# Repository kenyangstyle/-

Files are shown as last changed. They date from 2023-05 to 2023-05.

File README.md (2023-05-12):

# -
这是2023年华南理工大学机器人校内赛五山五狼—车车难造队的机械建模开源，我是本队机械建模队员 华南理工大学材料科学与工程学院 杨欣然。这次上传的车辆是自2023年2月得知赛题后便着手设计的，全部建模、图纸设计、加工联系任务和部分搭建任务由我完成。换句话说，我可以毫无任何内心压力的说我参与了前后两个队参赛的全过程，本车共有3代版本，每一代都是进行了相关的更新工作后进行，本次上传的便是第三代（也就是最终上场的车），十分不幸的是，由于一些完全超出本人能力的原因，最终上场参加2023-05-07和2023-05-13比赛的车与第三代车大相径庭。

底盘：
使用玻纤板，由4台545电机作为动力，橡胶轮4个，直径为96mm（未注明单位尺寸皆为毫米），前段为铲斗活动区，故仅在前后方安装铜柱；
中段与后段分别安装玻纤板作为连接，同时提供安装驱动板、电源板、电池等的空间，使用扎带固定电池/洞洞板
后段则安装了3D打印的滑梯，其中其高侧固定在铜柱、固定架上，低侧则搭在尾板舵机架（3D打印）上，作为承载木块的主要区域；尾板使用6mm玻纤板，在2台sg90舵机操作下进行移动，在规则改变后单独的舵机架被取消，舵机被固定在后方加固板上

抬升装置：
致敬VEX经典设计，但是玻纤板，前方用立柱（一个加工时给我带来了巨多麻烦的东西），大臂后方为齿轮组：2组4个20齿2模齿轮，其中下方2个齿轮与370电机D孔连接（这个主意现在来看蠢得一批），四个齿轮分别连接大臂上梁和小臂下梁，以抬升上方铲子。原计划小臂下梁使用活动滑梯版,承接铲子上的木块，后来由于改用铜柱加固，其已切割的板材被挪作他用。

铲子：铲子固定在抬升装置末端，用于提高位置，经过准确测量的铲子可完美覆盖3个矿区（如果抬升装置没bug的话），并通过一定角度顺利铲起木块，而在经过实际验证确认不可行后，在铲子两内侧加装了搂抱机构，可以将木块揽入其中，这一方案在实际测试中效果尚佳，但是对整体的电路稳定水平有较高要求。

取矿逻辑：车进入取矿区—车对准矿架—车抬起臂—铲子内机械臂揽入木块—机械臂抬升—铲子翻转90-130度，木块滑入活动滑梯版—木块从活动滑梯版划入固定滑梯板，并在碰撞尾板后停止-重复上述步骤到存储9-10个木块-车返回结算区-尾板翻转120-130度，木块凭借重力滑入并积分

反思：1、孔的设计：各个孔的尺寸并不统一，直接导致了在装车过程中零件（通用件）装配极为恶心，种类之繁多严重影响了我们的工作效率
      2、预留空间不足：整车设计上，由于几乎是贴着尺寸限制设计，许多原本在sw中显示无干涉的零件在实际装配和调试中纷纷出现干涉，最后不得不用角磨机处理
      3、零件选材：原本由于对行情不够了解，在设计底盘时选择L型铝，直接导致预算超标，被迫改设计改用玻纤，而在改图纸的过程中，由于对材料的不了解，预留孔位不够大，最后同样不得不上角磨机处理
      4、铲子：对矿物的错误理解直接导致了在测试过程中对木块的无能为力，而前段原本为铲起木块做的设计反而成为了破损的重灾区，幸运的是，铲面空间足够增加补救方案，遂加入2台舵机。
      5、储矿装置：同样出于对矿物的错误理解，使得矿物落入储矿机构后有掉落风险。但由于固定滑梯面和固定滑梯尾板是由3D打印制作，我们无法加高两侧防掉落机构，只能通过扎带进行软加固；同时原本的舵机臂设计由于舵机自身和规则改变的原因，先后剪短甚至弃用， 固定也最后选择打胶（正经的上热熔胶）。

未来改进：1、增加爬楼梯功能：由于时间关系，我们并没有安装爬楼梯的装置，而如果需要进行安装，完全可以在前轮电机和后轮电机中间加装2组4个伸缩电机，从而将前后轮组抬高
一半，从而上楼梯
          2、改用麦轮：原本寄希望于我们操作手的能力，但是在试车后认为麦轮还是有助于对准框架的，但是时间+尺寸原因导致其并未实现。
          3、铲子缩短：既然已经确认铲子无法铲木块，而必须要用揽的形式，则铲子也没必要做的过长，能放下舵机和揽入木块即可
          4、电机换成舵机：这是基于操作时难以控制升降臂两侧的电机同步行动而提出，实际上20kg360度舵机完全足够取代370电机，安装难度也有减小。
          5、统一孔径并加大预留空间：避免再出现由于各种尺寸螺丝螺母齐飞而导致的额外花费和效率低下，同时降低断孔概率

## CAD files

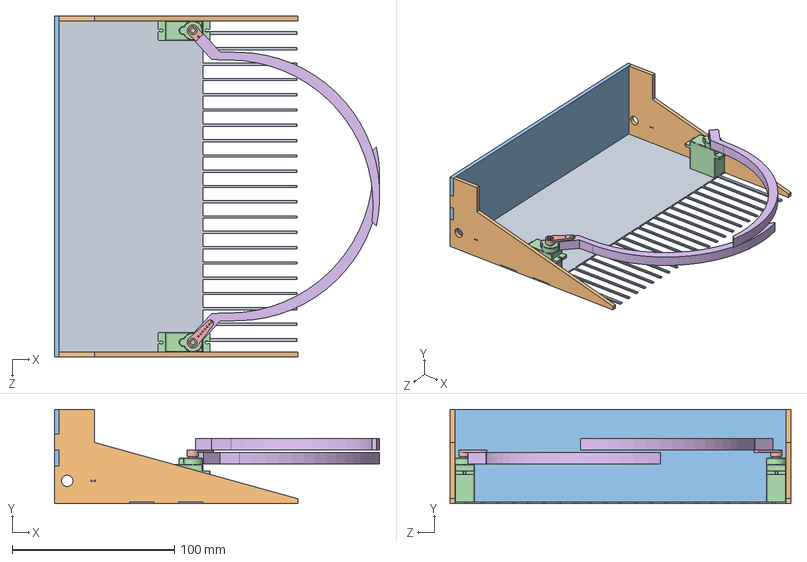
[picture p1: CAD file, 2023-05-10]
车车难造 最新机械开源/第二代应急铲子.SLDASM
200.4 x 58.0 x 210.0 mm
铲子 - 副本 (2)
铲子 - 副本 (3) x 2
铲子 - 副本
舵机 x 2
舵机臂 x 2
救急拉杆2 x 2

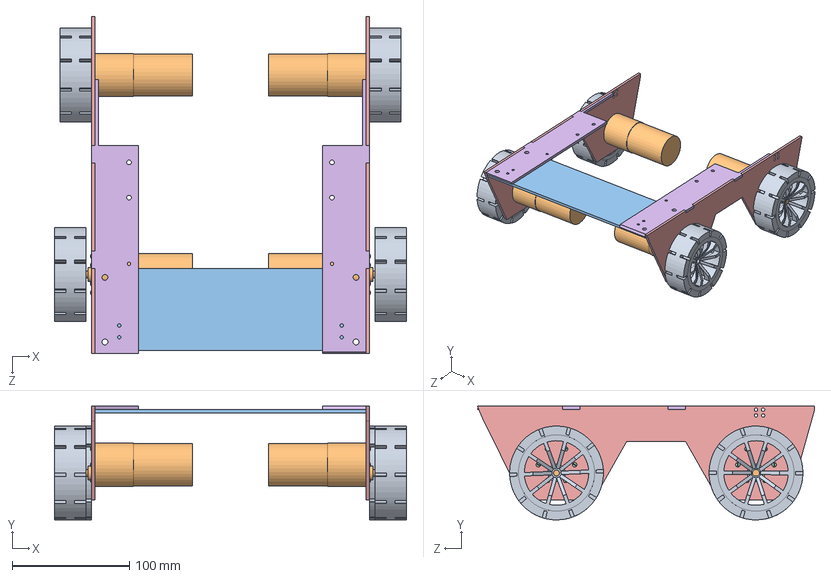
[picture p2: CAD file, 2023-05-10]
车车难造 最新机械开源/五山狼 第三代底盘原理.SLDASM
300.0 x 97.0 x 287.5 mm
teibielun x 4
545电机 x 4
下层结构加强
GB╱T 5284-1985[开槽半沉头自攻螺钉-F型ST2.2×6.5-F] x 24
L下插板 x 2
L上插板 x 2

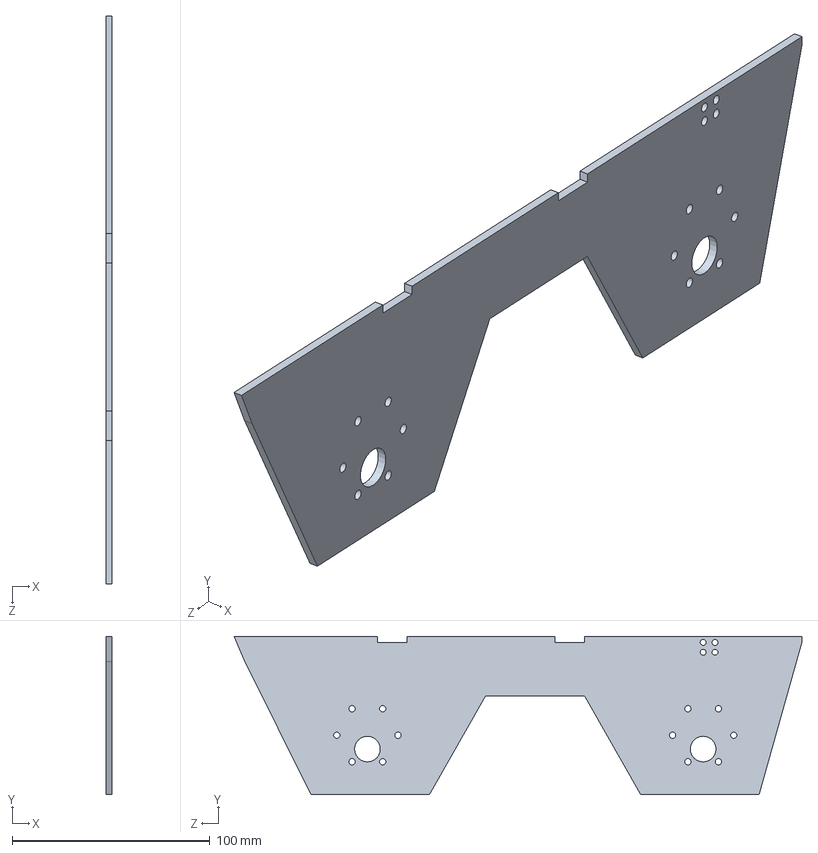
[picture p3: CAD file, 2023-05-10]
车车难造 最新机械开源/L--拼插板.SLDASM
3.00 x 80.0 x 287.5 mm

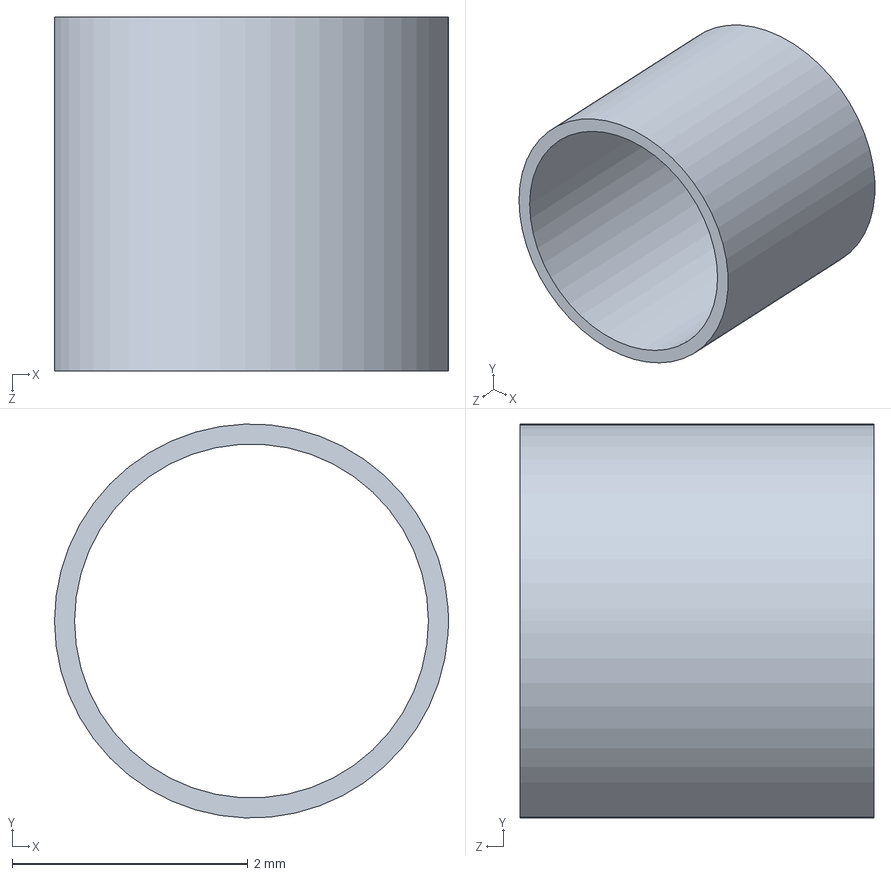
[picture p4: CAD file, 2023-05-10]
车车难造 最新机械开源/蠢得一批的轴套.SLDPRT
3.34 x 3.34 x 3.00 mm

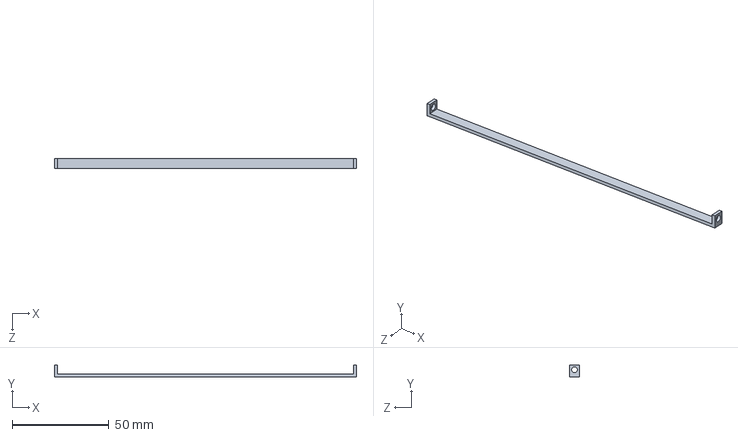
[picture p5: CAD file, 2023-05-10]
车车难造 最新机械开源/铝立柱（高.SLDPRT
156.0 x 6.00 x 5.00 mm

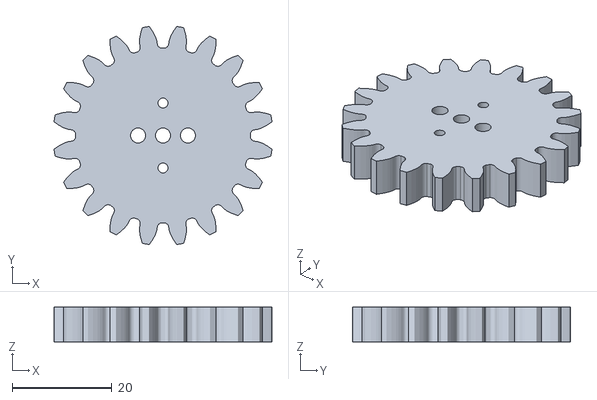
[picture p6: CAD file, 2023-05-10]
车车难造 最新机械开源/3代版本打印圆柱齿轮20×2.STL
43.7 x 43.7 x 7.00

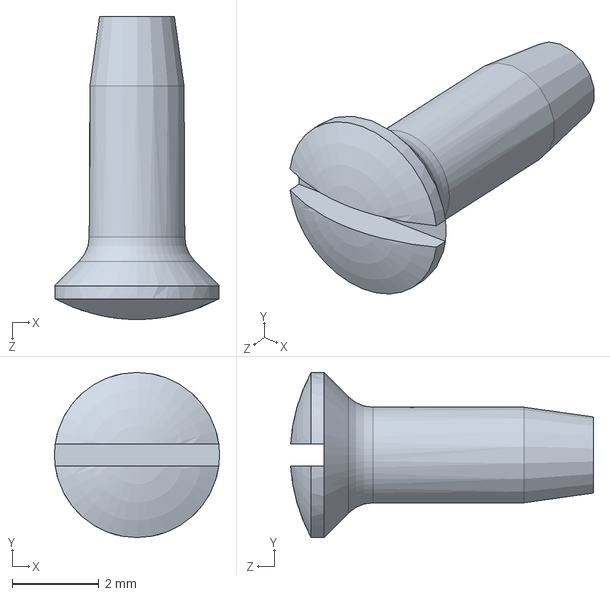
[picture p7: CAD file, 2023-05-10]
车车难造 最新机械开源/GB╱T 5284-1985[开槽半沉头自攻螺钉-F型ST2.2×6.5-F].sldprt
3.80 x 3.80 x 6.97 mm

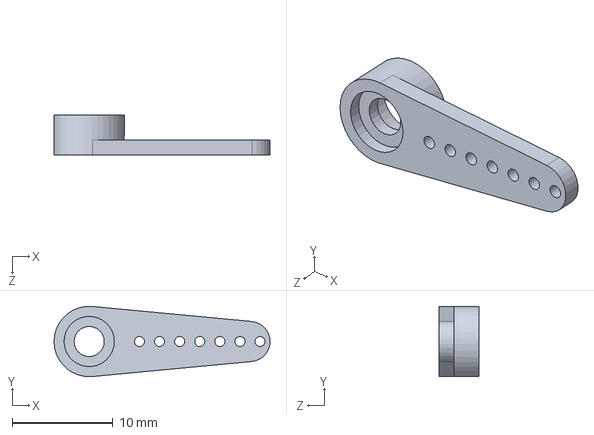
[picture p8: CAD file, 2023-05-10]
车车难造 最新机械开源/舵机臂.SLDPRT
21.5 x 6.99 x 4.00 mm

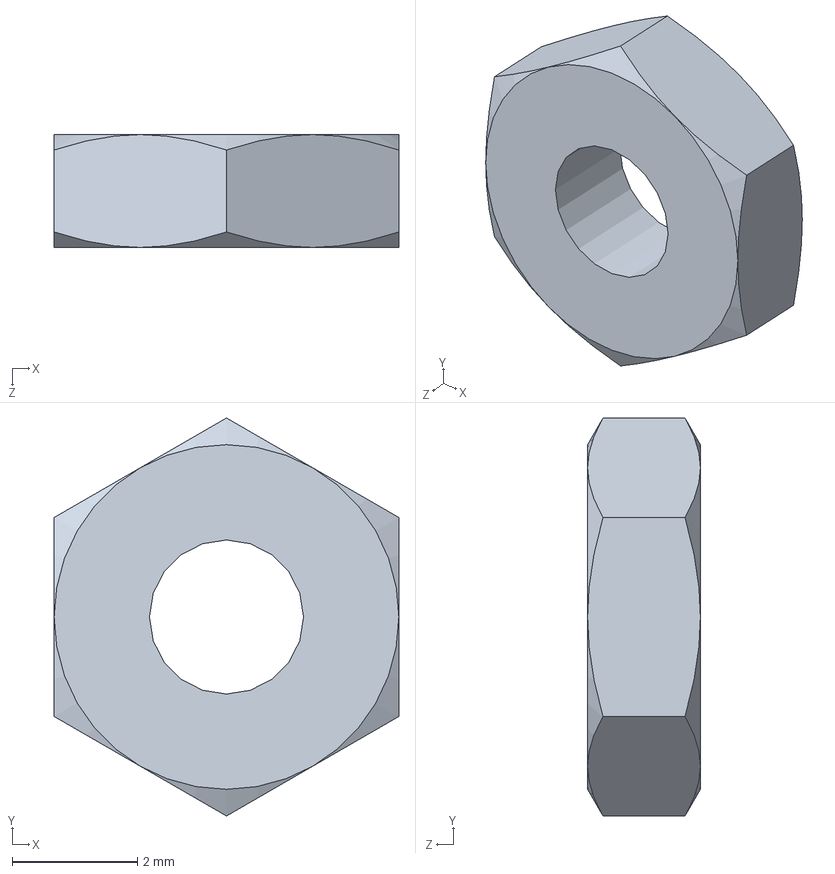
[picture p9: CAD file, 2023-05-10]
车车难造 最新机械开源/GB╱T 6172.1-2000[六角薄螺母 A级和B级M3].sldprt
5.50 x 6.35 x 1.80 mm

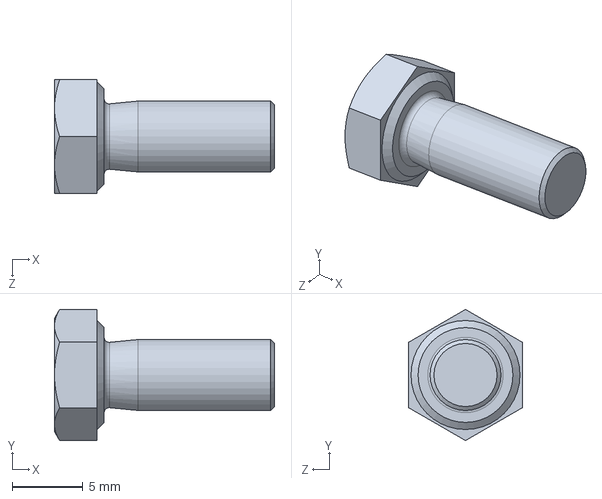
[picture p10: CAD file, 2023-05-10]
车车难造 最新机械开源/GB╱T 5783-2016[六角头螺栓 全螺纹M5×12].sldprt
15.5 x 9.24 x 8.00 mm

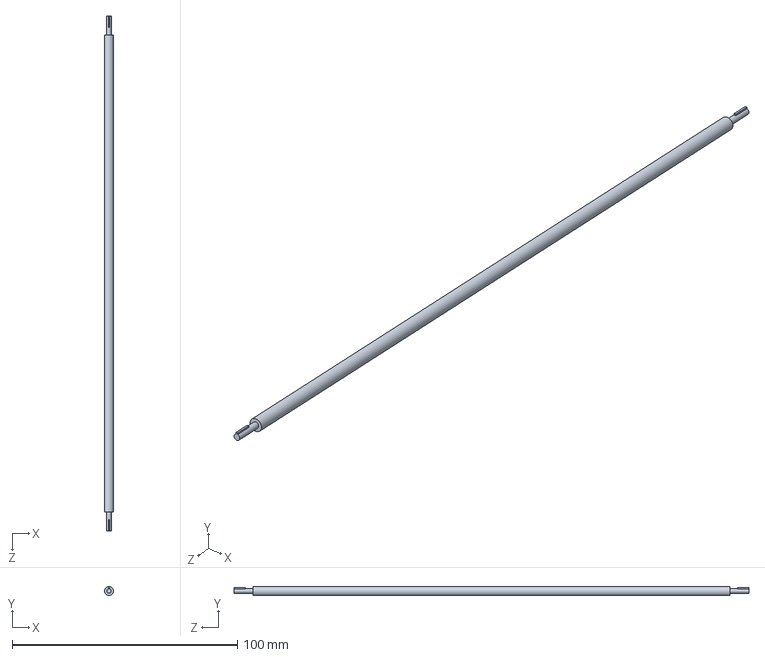
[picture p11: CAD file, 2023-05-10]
车车难造 最新机械开源/上方连接轴.SLDPRT
4.00 x 4.00 x 228.6 mm

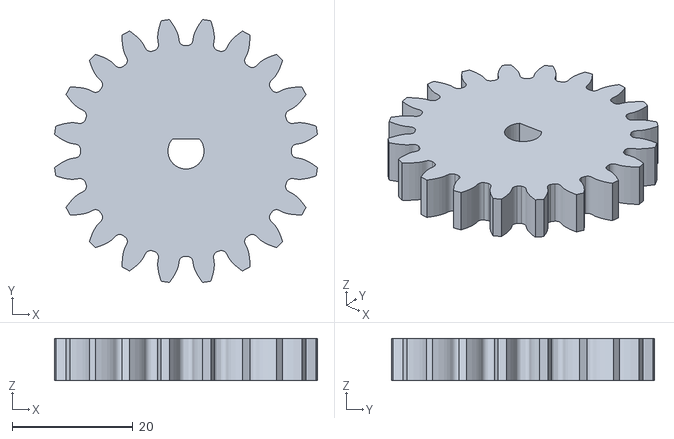
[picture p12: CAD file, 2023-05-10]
车车难造 最新机械开源/D孔圆柱齿轮20×2.STL
43.7 x 43.7 x 7.00

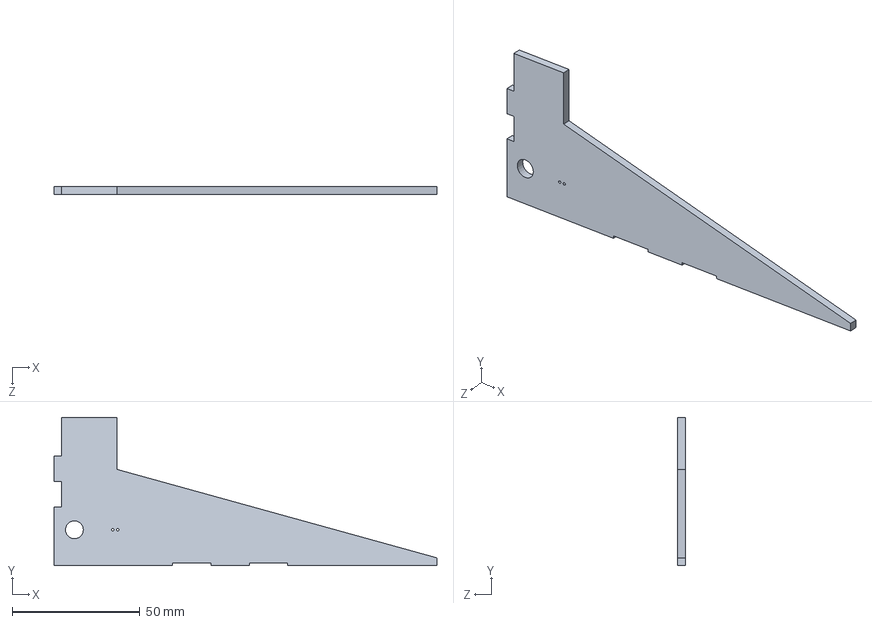
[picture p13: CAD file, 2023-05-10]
车车难造 最新机械开源/铲子 - 副本 (3).SLDPRT
150.0 x 58.0 x 3.00 mm

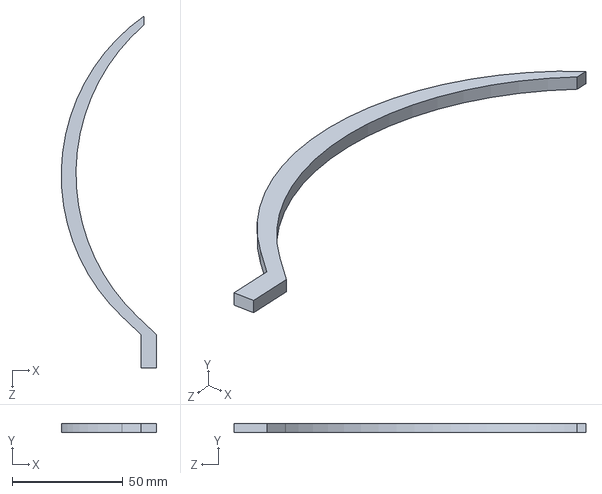
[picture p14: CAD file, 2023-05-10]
车车难造 最新机械开源/救急拉杆2.SLDPRT
43.1 x 4.00 x 159.2 mm

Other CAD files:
车车难造 最新机械开源/拼装版铲子.SLDASM
车车难造 最新机械开源/镜向铲侧板.SLDPRT
车车难造 最新机械开源/下方连接柱.SLDPRT
车车难造 最新机械开源/下层结构加强.SLDPRT
车车难造 最新机械开源/333圆柱齿轮20×2.STL
车车难造 最新机械开源/4444救急拉杆2.STL
车车难造 最新机械开源/545电机.SLDPRT
车车难造 最新机械开源/GB╱T 13806.2-1992[十字槽半沉头自攻螺钉 刮削端C ST1.9×4.5].sldprt
车车难造 最新机械开源/GB╱T 13806.2-1992[十字槽半沉头自攻螺钉 刮削端C ST2.9×5.5].sldprt
车车难造 最新机械开源/GB╱T 13806.2-1992[十字槽沉头自攻螺钉 刮削端B ST1.9×4].SLDPRT
车车难造 最新机械开源/GB╱T 13806.2-1992[十字槽盘头自攻螺钉 刮削端ST1.5×6].sldprt
车车难造 最新机械开源/GB╱T 13806.2-1992[十字槽盘头自攻螺钉 刮削端ST1.5×7].sldprt
车车难造 最新机械开源/GB╱T 41-2000[六角螺母C级M5].sldprt
车车难造 最新机械开源/GB╱T 5783-2000[六角头螺栓 全螺纹M3×25].sldprt
车车难造 最新机械开源/GB╱T 5783-2016[六角头螺栓 全螺纹M3×12].sldprt
车车难造 最新机械开源/GB╱T 5783-2016[六角头螺栓 全螺纹M4×8].sldprt
车车难造 最新机械开源/GB╱T 5783-2016[六角头螺栓 全螺纹M5×10].sldprt
车车难造 最新机械开源/GB╱T 6170-2000[1型六角螺母 A级和B级M3].sldprt
车车难造 最新机械开源/GB╱T 6170-2000[1型六角螺母 A级和B级M4].sldprt
车车难造 最新机械开源/GB╱T 6174-2016[六角薄螺母 无倒角M3].sldprt
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
